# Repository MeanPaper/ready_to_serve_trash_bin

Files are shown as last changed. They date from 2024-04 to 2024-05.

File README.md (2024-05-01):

# Ready-to-serve Trash Bin
By collaboration of [Dongming Liu](https://github.com/MeanPaper), [Owen Xu](https://github.com/jinyuxu2), [Josh Litao](https://github.com/jlitao2) <br>
UIUC SP24 Senior Project Repository (Team 19) | January 2024 - May 2024

## About the Project
Throwing away trash is a simple task that many people take for granted. However, those with little to no mobility as a result of a disability, hospitalization, natural aging, or other health conditions struggle to carry out this necessary task. According to the CDC, 12.1 percent of U.S. adults have a mobility disability with serious difficulty walking or climbing stairs. As a result, these people either require an assistant to dispose of their trash for them, which may not always be feasible, or they are forced to hold their trash and let it accumulate by their side. Letting trash accumulate is a sanitary concern that could escalate into further problems. A trash bin could be placed next to the person, but this solution has various problems. An open trash bin would allow the odor of the trash to spread throughout the room, and a bin with a lid could pose difficulty for users whose conditions make them unable to open the lid directly with their hands or use their foot to press the pedal.

In order to eliminate the problems with existing trash bins for people with limited mobility, we propose a trash bin that would be ready to take a user’s trash once they perform a particular hand gesture to call it. A camera will be part of the motion and object detection system. This system to detect the hand gesture would be placed somewhere in the room where it would be able to monitor whether the user needs the trash bin to pick up their trash. The trash bin would be attached to a set of wheels to allow it to move. The lid of the bin would also be controlled to open and close. Once the camera detects that the user wishes to dispose of trash, the camera system would wirelessly communicate with the bin to prompt the bin to move toward the user. Upon arriving at the user, the lid would open, ready to collect the user’s trash. Once the user has disposed of trash into the bin, the lid would close, and the bin would return to its resting position. This solution simplifies the process of throwing trash by only requiring the users to call it and drop their trash into the bin.

## Project Video and Presentation
[Video](https://www.youtube.com/embed/DfU_nMM2fV8)<br>
[Presentation](https://courses.engr.illinois.edu/ece445/getfile.asp?id=23341)

## Usage 
### Hand Gesture Detection
For hand gesture detection, we recommend [Raspberry Pi 4B with 4GB RAM](https://www.raspberrypi.com/products/raspberry-pi-4-model-b/) with [64-Bit Raspberry Pi OS](https://www.raspberrypi.com/software/operating-systems/). The project uses this [Pi Camera](https://www.amazon.com/Arducam-Megapixels-Sensor-OV5647-Raspberry/dp/B012V1HEP4?th=1) in our project but other Pi Camera or USB camera should work as well. 

The required packages for the hand gesture detection can be found [here](https://github.com/MeanPaper/ready_to_serve_trash_bin/blob/main/hand-gesture-recognition-mediapipe/README.md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). To make package installation easier, we recommend setting up a virtual python environment using [`conda`](https://conda.io/projects/conda/en/latest/user-guide/getting-started.html) or [`venv`](https://docs.python.org/3/tutorial/venv.html). 

### Running Hand Gesture Detection and Training
More details can be found in the [hand-gesture-recognition-mediapipe](https://github.com/MeanPaper/ready_to_serve_trash_bin/blob/main/hand-gesture-recognition-mediapipe/README.md).

## Acknowledgements
- [Hand guesture recognition mediapipe](https://github.com/kinivi/hand-gesture-recognition-mediapipe/tree/main): computer vision for hand guesture recognition.
- [COMTool](https://github.com/Neutree/COMTool): easy-to-use debugging tool, for gathering data from serial port.

## References
- [QuickPID](https://github.com/Dlloydev/QuickPID/tree/master)
- [ESPAsyncWebServer](https://github.com/esphome/ESPAsyncWebServer)
- [ESP-IDF Programming Guide](https://docs.espressif.com/projects/esp-idf/en/stable/esp32s3/index.html)
- [ESP32-S3-WROOM-1 Datasheet](https://www.espressif.com/sites/default/files/documentation/esp32-s3-wroom-1_wroom-1u_datasheet_en.pdf)
- [L298](https://www.st.com/content/ccc/resource/technical/document/datasheet/82/cc/3f/39/0a/29/4d/f0/CD00000240.pdf/files/CD00000240.pdf/jcr:content/translations/en.CD000002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)
- [TPS56220x 4.5V to 17V Input, 2A Synchronous Step-Down Voltage Regulator in SOT-23](https://www.ti.com/lit/ds/symlink/tps562201.pdf)
- [TLV1117LV 1-A, Positive Fixed-Voltage, Low-Dropout Regulator](https://www.ti.com/lit/ds/symlink/tlv1117lv.pdf)
- [Low Dropout Linear Regulator](https://www.diodes.com/assets/Datasheets/AZ1117C.pdf)

## Academic Integrity
Please review the University of Illinois Student Code, particularly all subsections of [Article 1, Part 4 - Academic Integrity Policy and Procedure](https://studentcode.illinois.edu/article1/part4/1-401/).

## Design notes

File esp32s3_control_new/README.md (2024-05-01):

# MCU Code

## Pins (GPIOs) Setting
The pin settings are listed in `Proj_Setup.h`.

## WiFi Configuration
Change the following two lines in `esp32s3_control_new.ino` to let the MCU connect to different WiFi.
```cpp
const char * ssid = "your_actual_wifi_name"; 
const char * pass = "your_actual_wifi_password"; // if there is no wifi password, make it NULL
```
For retriving the MAC address of the MCU, use `WiFi.macAddress()`.

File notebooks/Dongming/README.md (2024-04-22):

# Dongming's Development Log

## Table of Contents
- [Dongming's Development Log](#dongmings-development-log)
  - [Table of Contents](#table-of-contents)
  - [Feburary 12, 2024](#feburary-12-2024)
    - [Project Design: Project Components](#project-design-project-components)
  - [Feburary 16, 2024](#feburary-16-2024)
    - [Project Design: Component Update](#project-design-component-update)
  - [February 20, 2024](#february-20-2024)
    - [Project Design: Motor Choice](#project-design-motor-choice)
  - [Feburary 27, 2024](#feburary-27-2024)
    - [MCU Code: Begin](#mcu-code-begin)
  - [March 02, 2024](#march-02-2024)
    - [MCU Code: MCU Pin Info and Driver Usage](#mcu-code-mcu-pin-info-and-driver-usage)
  - [March 04, 2024](#march-04-2024)
    - [MCU Code: Code Struture and MCU Pin Assignments](#mcu-code-code-struture-and-mcu-pin-assignments)
  - [March 09, 2024](#march-09-2024)
    - [MCU Code: Wireless Communication Code](#mcu-code-wireless-communication-code)
  - [March 13, 2024](#march-13-2024)
    - [MCU Code: Wireless Communication Testing Part 1](#mcu-code-wireless-communication-testing-part-1)
  - [March 16, 2024](#march-16-2024)
    - [MCU Code: FSMs](#mcu-code-fsms)
  - [March 17, 2024](#march-17-2024)
    - [MCU Code: Wireless Communication Testing Part 2](#mcu-code-wireless-communication-testing-part-2)
  - [March 18, 2024](#march-18-2024)
    - [MCU Code: Motor Control Code](#mcu-code-motor-control-code)
  - [March 26, 2024](#march-26-2024)
    - [Debug Customized PCB: Unable to Upload code to MCU with USB-to-UART](#debug-customized-pcb-unable-to-upload-code-to-mcu-with-usb-to-uart)
  - [March 29 to March 31, 2024](#march-29-to-march-31-2024)
    - [MCU Code: Motor Control - PID tunning](#mcu-code-motor-control---pid-tunning)
  - [April 05, 2024](#april-05-2024)
    - [PCB Testing: PCB v1](#pcb-testing-pcb-v1)
  - [April 08, 2024](#april-08-2024)
    - [PCB Testing: PCB v1 motor driver port two](#pcb-testing-pcb-v1-motor-driver-port-two)
    - [Project Design: Minor Update on Physical Design](#project-design-minor-update-on-physical-design)
  - [April 10, 2024](#april-10-2024)
    - [Project Production: Assembling and Testing](#project-production-assembling-and-testing)
  - [April 12, 2024](#april-12-2024)
    - [Project Production: Assembling Checklist](#project-production-assembling-checklist)
  - [April 17, 2024](#april-17-2024)
    - [Project Production: Product Testing without Raspberry Pi](#project-production-product-testing-without-raspberry-pi)
  - [April 18, 2024](#april-18-2024)
    - [Project Production: 3D Printed Box](#project-production-3d-printed-box)
  - [April 19, 2024](#april-19-2024)
    - [Project Production: Intergration Testing Part 1](#project-production-intergration-testing-part-1)
  - [April 20, 2024](#april-20-2024)
    - [Project Production: Intergration Testing Part 2](#project-production-intergration-testing-part-2)
  - [April 21, 2024](#april-21-2024)
    - [Project Production: Demo Setup](#project-production-demo-setup)
  - [EXTRA NOTE](#extra-note)

## Feburary 12, 2024
### Project Design: Project Components

Ready-to-serve trash bin has two big systems
- Motion and Object Detection System
- Trash Bin Control System

**Motion and Object Detection System:**
| Component | Usage |
| :--- | :--- |
| Raspberry Pi  | Image processing and communication with Trash Bin Control System  |
| Pi Camera | Image Capturing |

The Raspberry Pi Models I considered using:
- Raspberry Pi 4B RAM 4GB or 8GB
- Raspberry Pi 5 RAM 4GB or 8GB

Alternative to Raspberry Pi:
- OrangePi 4 / 5 with RAM 4GB or 8GB

If Raspberry Pi is not powerful enough, then the following would be considered:
- Nvidia Jetson board
- Intel processor single board computer
  
<br>

**Trash Bin Control System:**
| Component | Usage |
| :--- | :--- |
| [ESP32S3 WROOM 1 N16 ](https://www.espressif.com/sites/default/files/documentation/esp32-s3-wroom-1_wroom-1u_datasheet_en.pdf) | Wireless communication, control and drive motors with PWM signals |
| [L298N](https://www.digikey.com/en/products/detail/stmicroelectronics/L298N/585918) | Motor driver chip for amplifying the PWM from MCU based on the reference volatge |
| 12V DC Gear Motors (reversible) | Move the trash bin on the floor |
| 12V Linear Actuator (reversible)  | Open and close trash bin's lid  |

ESP32S3 WROOM 1 has a built-in wireless communication module; it is a good fit for this project. This MCU is part of the ESP32 S-series.<br>
***The alternative MCUs*** are still based on ESP32 but are in different series, for example, C-series or H-series.

The Motor driver chip L298N is very popular. One chip can control up to 2 DC motors. L298N supports up to a rated voltage of 40V and a max current of 2A, which is more than enough. L298N is hard to solder due to its package. Also, L298N is relatively expensive. <br>
***The alternative motor drivers*** are [A4950](https://www.digikey.com/en/products/detail/allegro-microsystems/A4950ELJTR-T/2626340) or [DRV8870](https://www.digikey.com/en/products/detail/texas-instruments/DRV8870DDAR/5455925). Both have wide operating ranges. The drawback is that each motor driver can only control 1 motor.

The 12V linear actuator only does 3 motions: open, hold, and close. Position tracking is not necessary, so the 12V linear actuator only needs to has two terminals.

The 12V DC Motors needs to provide speed tracking interfaces. One mechanism of speed tracking will be to used hall encoders. 

The power subsystems for these two big systems are ignored. My teammate will come with the power circuit/subsystem for the project.

**TODO:**
- Finalize all components for this project (not including battery)
- Learn how to detect speed using hall encoders
- Skim through the data sheet of ESP32S3 and get familiar with the pins on ESP32S3

## Feburary 16, 2024
### Project Design: Component Update

**Updates:**
- Raspberry Pi 4B with 4 GB. The system is Raspberry Pi OS (64-bit)
- Camera module (5M pixel somana camera module with OV5647)
- Power for Raspberry Pi: Raspberry Pi 4 official charger
- 12V linear actuator is finalized. The part and its purchase link are updated in the component list. 
- 12V DC motors are finalized. The part and its purchase link are updated in the component list. JGB37-520 Hall Encoder Miniature Brushed DC Motor (178 RPM).

The MCU code will be developed on a development board with ESP32S3-WROOM-1-N8 module. For motor drivers, I will use the L298N breakout boards. 

Tentative setup for the project testing:
| Components | Quantity |
| :--- | ---: |
| ESP32S3-WROOM-1 Dev Board | 1 |
| L298N module | 2 |
| Breadboard | 1 |
| Jumper wires | 30 |

Note: the jumper wires might be a bit more, but they are for rewiring.

## February 20, 2024
### Project Design: Motor Choice

The motor needs to provide enough power to move the bin. Therefore, we need to come up with a minimum theoretical power of a motor.

|  Variable  | Comment |
|:--- |:---|
| $\tau_{w}$ | torque of a motor (in Nm) |
| $R_{w}$ | wheel radius (in m) |
| $\mu_{w}$  | static friction coefficient of the wheel against the floor |
| $\mu_{c}$  | static friction coefficient of the metal caster against the floor|
| $m_{T}$ | total mass (in kg) |
| $F_{N}$ | normal force (in N) |
| $F_{wf}$ | static friction of the wheel (in N) |
| $F_{cf}$ | static friction of the mastern (in N) |
| $g$ | gravitational acceleration constant (m/s<sup>2</sup>) |

Two DC gear motors at the same position can provide:

$2\tau_{w}=F_{wf} * R_w$

In rolling without slipping, the static friction of the wheels cannot exceed the static friction of the total mass. With two type of wheels (one in rubber, and the other in metal), we have:

$F_{wf} \leq F_N * (\mu_w + \mu_c)$

Using Newton's Second Law:

$F_g = m_T * g$

since the bin does not accelerate up and/or down, $F_g = F_N$

Therefore, the static friction of the total mass is:

$m_T * g * (\mu_w+\mu_c)$

Combing the inequality:

$\frac{2\tau_w}{R_w} \leq m_T * g * (\mu_w + \mu_c)$

$\frac{2\tau_w}{R_w * g * (\mu_w + \mu_c)} \leq m_T$

The wheel radius of our wheel is about 0.0762 m. Assuming that the static coefficients of both wheels are approximately 0.5, and the total mass is about 2.3kg to 2.8kg, we need both motors to provide a torque of at least 0.373 Nm.

Also, we want the bin to move at human walking speed, which should be no more than 1.2 m/s. 

$\text{motor RPM} \leq \frac{1.2 * 60}{\pi * d}$

Based on the theoretical result, the motor we picked previously might not be able to move the bin. So we switch to JGB37-520 Hall Encoder Miniature Brushed DC Motor (60 RPM).

## Feburary 27, 2024
### MCU Code: Begin

MCU code quick break down:
- Motor control module
    - DC motors
    - linear actucator
- Wireless communication module
    - WiFi
    - Service API

The DC motors need to use 5 pins (`PWM`, `D1`, `D2`, `HALL_A`, `HALL_B`)
| Pin Name  | Description |
| :---: | :--- |
| `PWM` | PWM signal to the motor driver|
| `D1`  | Direction control 1 (for H-bridge) to the motor driver|
| `D2`  | Direction contorl 2 (for H-bridge) to the motor driver|
| `HALL_A` | Hall encoder phase A from the motor|
| `HALL_B` | Hall encoder phase B from the motor|
  
The linear actuator need to use 3 pins (`PWM`, `D1`, `D2`)
| Pin Name  | Description |
| :---: | :--- |
| `PWM` | PWM signal to the motor driver|
| `D1`  | Direction control 1 (for H-bridge) to the motor driver|
| `D2`  | Direction contorl 2 (for H-bridge) to the motor driver|

**Quick Review on H-bridge:** <br>
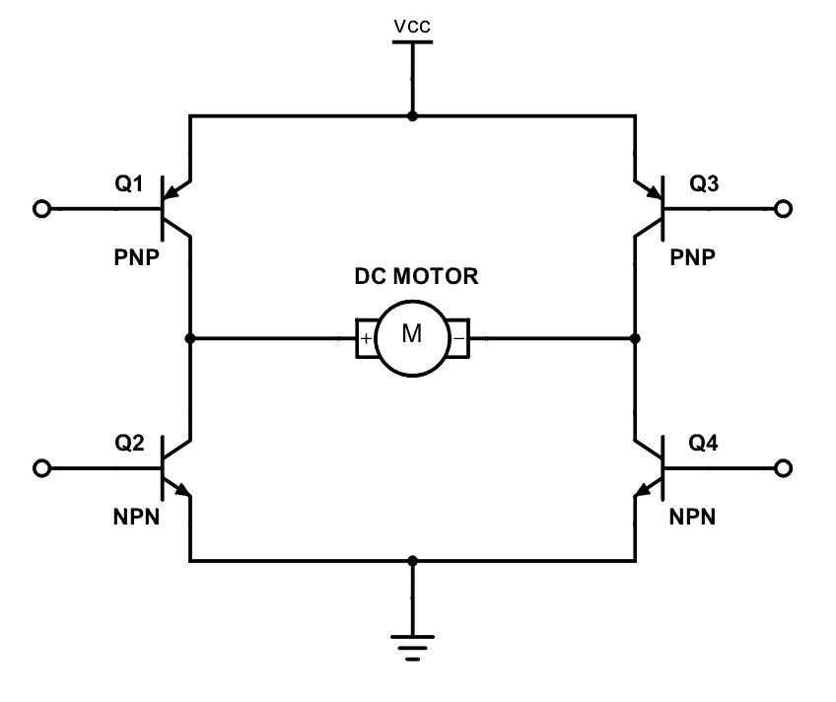
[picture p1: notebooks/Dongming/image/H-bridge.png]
H-bridge Schematic

<br>
`Q1` and `Q4` are controlled by one of the `D`'s; `Q2` and `Q3` are controlled by the other `D`. If `Q1 = Q4 = HIGH` and `Q2 = Q3 = LOW` makes the motor turn clockwise (assuming), then `Q1 = Q4 = LOW` and `Q2 = Q3 = HIGH` makes the motor turn counterclockwise.

In [L298N](https://www.st.com/content/ccc/resource/technical/document/datasheet/82/cc/3f/39/0a/29/4d/f0/CD00000240.pdf/files/CD00000240.pdf/jcr:content/translations/en.CD000002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), it has two H-bridges. The IN1 and IN2 (or IN3 and IN4) can be mapped to D1 and D2. The MCU can send logic HIGH and LOW via D1 and D2. This effectively controls the state of each pair of switches, similar to the previous description.

**Quick Review on PWM** 
<br>
With PWM control, we can limit the voltage (and current) delivered to the motors and linear actuators. 
<br>
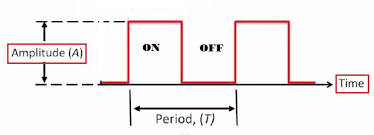
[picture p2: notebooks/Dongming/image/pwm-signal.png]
PWM signal diagram


The Duty cycle is the percentage of ON time with respect to the entire period (like the diagram shown above). So,

$\text{Duty Cycle} = \frac{T_{ON}}{T_{Period}}$

and the average voltage over time is

$V_{avg} = \text{Duty Cycle} * V_{amplitude}$

For example, given the max voltage is 12V and the duty cycle is 50%, the average voltage will be 6V. 

With PWM control and constant DC source, we can change the voltage delivered by changing the duty cycle of the PWM signal, allowing the motors and linear actuators to run at different speeds.

**Quick Start on Hall Encoder**

One popular speed measuring method is to use the hall encoders. Most DC motors with hall encoders have two phases: A and B. 

By observing the difference between the two phases, we can determine the direction the motors are turning and approximate the speed of the motors. One method is 

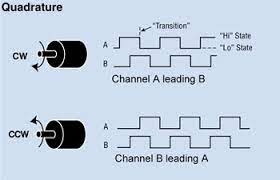
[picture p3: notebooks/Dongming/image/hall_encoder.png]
Quadrature hall encoder


An nice article on Speed Measurement (in Chinese): https://zhuanlan.zhihu.com/p/350368518

I will use the M-method for speed measurements. The unit of speed is RPM.

The computation can be done as the following:

$\text{total pulse count} = \text{PPR} * \text{reduction ratio}$

$\text{output shaft speed} = \frac{\text{pulse count}}{\text{total pulse count}} * \frac{1000}{\text{sample time (ms)}} * 60$

This computation will approximate the current speed of the motors (in RPM) based on the pulse counts.

**TODO:**
- Set up wireless communication between the ESP32S3 chip and other edge devices
- Figure out how to control motor using L298N

## March 02, 2024
### MCU Code: MCU Pin Info and Driver Usage

**Quick Check of ESP32S3-WROOM-1**

The official documentation of ESP32S3-WROOM-1: https://www.espressif.com/sites/default/files/documentation/esp32-s3-wroom-1_wroom-1u_datasheet_en.pdf

The technical manual of ESP32S3-WROOM-1: https://espressif.com/documentation/esp32-s3_technical_reference_manual_en.pdf

Some pins might not be available for programming:

For modules with Octal SPI PSRAM, i.e., modules embedded with ESP32-S3R8 or ESP32S3R16V, pins IO35 (GPIO 35), IO36 (GPIO 36), and IO37 (GPIO 37) are connected to the Octal SPI PSRAM and are not available for other uses.

Strapping pins are used to set up the MCU mode:
- Chip boot mode -- GPIO 0 and GPIO 46
- VDD_SPI voltage -- GPIO 45 
- ROM messages printing -- GPIO 46 
- JTAG signal source -- GPIO 3

Section 3.3.1 specifies the download mode setup for the MCU. GPIO 0 needs to be set to logic low to enable Joint Download Boot (maybe we need to have some connections in the schematic to configure the MCU mode)

Section 3.3.4 specifies the setup of the GPIO 3 for enabling JTAG (useful for debugging).

Avoid using GPIO 39 and above. Jtag uses GPIO 39 ~ 41. GPIO 42 and 43 are used for downloading code. We will use a USB-to-UART bridge module to manage auto-download rather than solder a bridge IC on board.

Something need to pay attention when using WiFi ([A useful website](https://nu-ll.github.io/2022/06/05/ESP32%E5%BC%95%E8%84%9A%E4%BD%BF%E7%94%A8%E6%B3%A8%E6%84%8F%E4%BA%8B%E9%A1%B9/))

GPIOs associated with ADC2 channels may be occupied when WiFi is in use. If our MCU cannot read/write to those pins when WiFi is enabled, we need to use some other pins. GPIOs associated with ADC1 channels can be an alternative in case that we need to use the ADC functionalities or use them for other purposes.

ESP32S3 have two different wireless communication method between devices (assuming the other device is not a ESP32 board).
- Bluetooth (normal bluetooth / low power bluetooth)
- WiFi 

The WiFi communication generally has a wider range. So it would be a good option in our case. To make the communication more standardized, I will use HTTP protocols. HTTP protocols are built on top of TCP, and TCP can minimize packet loss in our communication. However, the efficiency of wireless communication might decrease a bit. An alternative would be using UDP. UDP can provide great efficiency under good network conditions but may result in a larger packet loss if the network conditions are not desired.

**L298N setup**

L298N Datasheet: https://www.st.com/resource/en/datasheet/l298.pdf

The L298N is a dual full-bridge driver. Inside L298N, there are two full H-bridge drivers. Previously, I have investigated [how H-bridge works](#mcu-code-begin), I can just connect the IC based on that. Since I was not too familiar with power circuit, I handed this part to my EE teammate. 

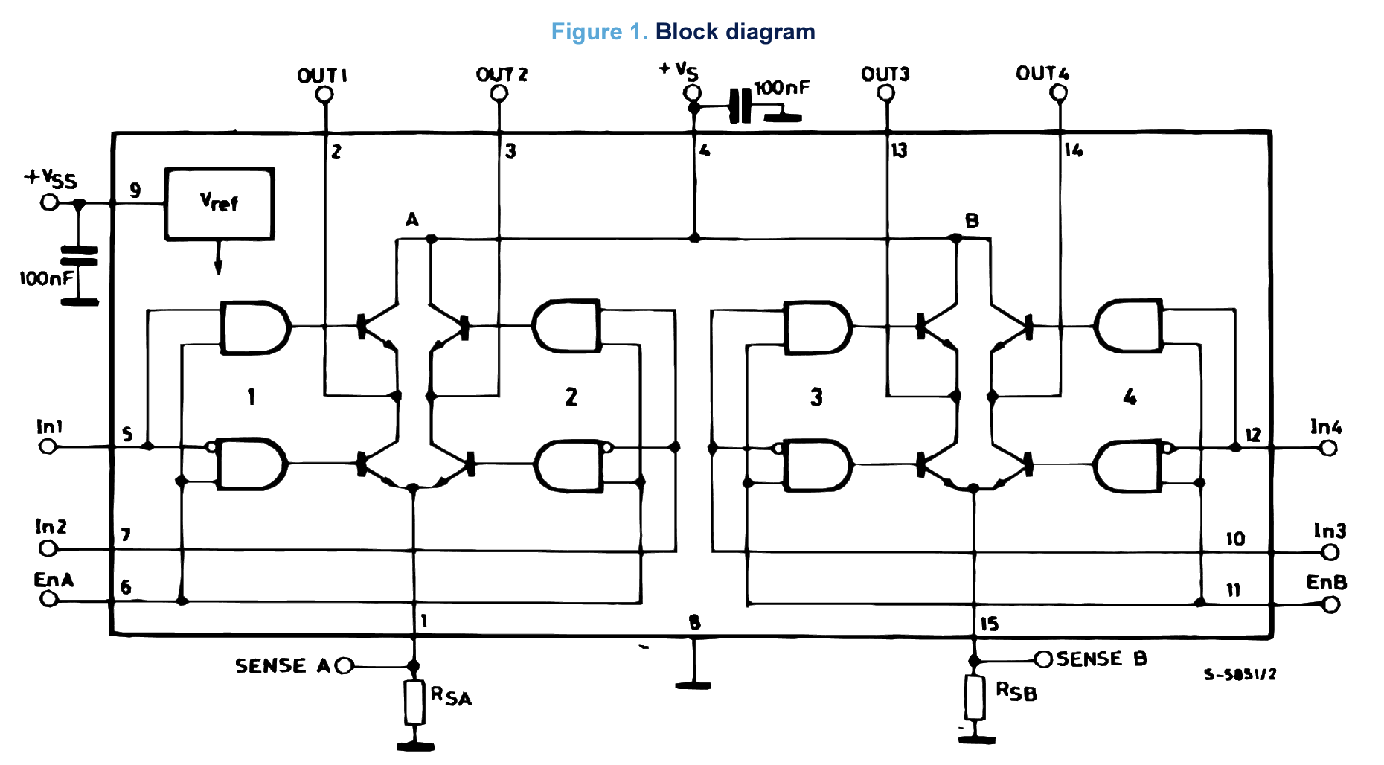
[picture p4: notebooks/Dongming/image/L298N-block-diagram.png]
L298N block diagram


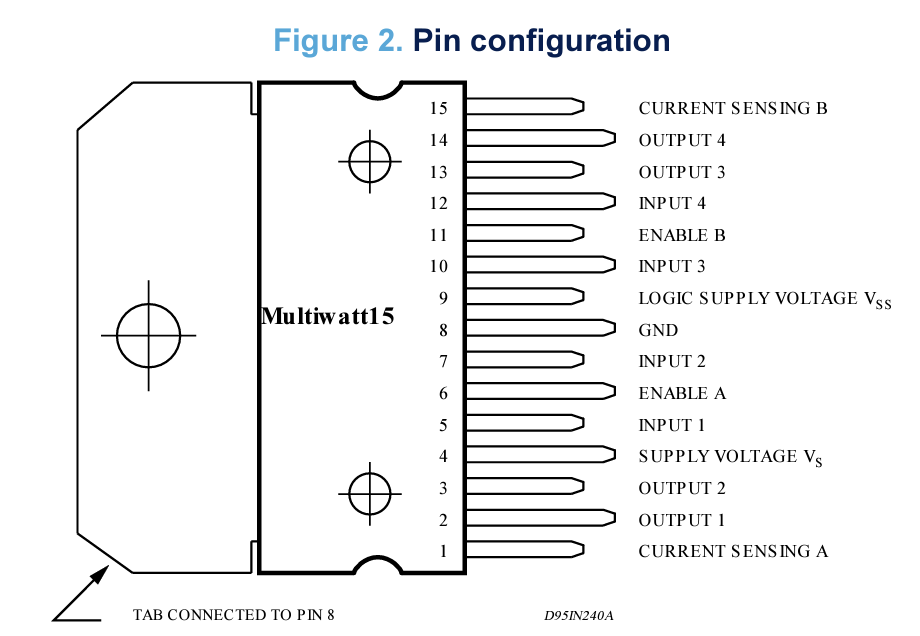
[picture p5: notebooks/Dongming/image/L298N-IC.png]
L298N IC


ENABLE A, IN 1, IN 2, OUTPUT 1, and OUTPUT 2 control the first motor. <br>
ENABLE B, IN 3, IN 4, OUTPUT 3, and OUTPUT 4 control the second motor.

The IN's control the direction of the motors. ENABLE's determine if the motor should be running of not. It is recommended to drive the ENABLE's with PWM to achieve speed control. OUTPUT's control the current outputing to the motors.

**TODO:**
- Assign MCU pins for programming
- Draft the wireless communication for the MCU

## March 04, 2024
### MCU Code: Code Struture and MCU Pin Assignments 

Files and brief:
- `esp32s3_control_new.ino`: main function, containing initial set up, MCU loop, and other main loop related variables/ helper functions/ handlers.
- `DCMotor.h`: a header file, containing a DCMotor class
- `DCMotor.cpp`: contains all function definitions of DCMotor class
- `Proj_Setup.h`: a header file, containing MACROS, enum, structures, and all helper functions in the projects
- `Proj_Setup.cpp`: contains all function definitions of helper functions and global variables 

Here is the finalized version of the pin assignments
```cpp
/**
  * DC Motor Control 
  * MT# = motor #
  * D1 and D2 are used for H-bridges control
  * D1 (out) - motor direction control 1
  * D2 (out) - motor direction control 2
  *
  * HALL_A and HALL_B are the pins for motor hall sensors, 
  * used for determining motor speed and direction
  * HALL_A (in) - hall sensor phase A
  * HALL_B (in) - hall snstor phase B
  *
  * PWM is the PWM signal for the motor driver, voltage/speed control 
  * PWM (out) - output 
  *
  */

// motor 1 control pins
#define MT1_D1      11
#define MT1_D2      12
#define MT1_PWM     13
#define MT1_HALL_A  16
#define MT1_HALL_B  18

// motor 2 control pins
#define MT2_D1      38
#define MT2_D2      35
#define MT2_PWM     14
#define MT2_HALL_A  17
#define MT2_HALL_B  21

/**
  * Linear Actuator
  * D1 and D2 are used for H-bridges control
  * D1 (out) - motor direction control 1
  * D2 (out) - motor direction control 2
  *
  * PWM is the PWM signal for the motor driver, voltage/speed control 
  * PWM (out) - output 
  *
  */
// linear actuator pins 
#define Ln_Act_D1   36
#define Ln_Act_D2   37
#define Ln_Act_PWM  15
```
The GPIOs listed here will connect to the corresponding components on the customized PCB.

In ESP32, the LED control (LEDC) peripheral is primarily designed to control the intensity of LEDs, but it can also be used to generate PWM signals. The PWM controller can automatically increase or decrease the duty cycle gradually, allowing for fades without any processor interference. We can control PWM output frequency, resolution, and channels of LEDC in setup to ensure that the PWM is tailored to the project's components. The library header is `esp32-hal-ledc.h`. In Arduino-ESP32 core, we can use `analogWrite` (a function in Arduino Analog I/O) to output PWM signals on a specific pin. However, the Arduino Analog I/O only has a few parameters can be configured. 

```cpp
/* PWM control section */

// PWM channels
#define CHAN_MT_ONE 1
#define CHAN_MT_TWO 2
#define CHAN_LN_ACT 3

// PWM control params
#define RESOL   8                 // resolution of the PWM signal
#define MT_FREQ 200               // motor channel frequency, this may not work
#define LA_FREQ 200               // linear actuator frequency
#define MAX_PWM pow(2, RESOL)-1   // the max duty cycle
```
**TODO:**
- Draft the wireless communication for the MCU

## March 09, 2024
### MCU Code: Wireless Communication Code

The wireless communication can be break into 3 steps:
1. MCU establishes a WiFi connection (with a device/router)
2. MCU creates a web server with different APIs 
3. MCU listens for requests coming from the client device (in the project, the client device is the Raspberry Pi)

**WiFi Connection**

Arduino IDE's built-in library `WiFi` can help ESP32S3 establish a WiFi connection with a router or make ESP32S3 a WiFi access point. The `WiFi` class has two modes `softAP` and `STA`.
- `softAP`: makes ESP32S3 a WiFi access point
- `STA`: ESP32S3 will connect to the WiFi router

`STA` is more suitable for the project. Since ESP32S3 is connected to a WiFi router, and the WiFi router's signal is strong, ESP32S3 can communicate with the WiFi router pretty much everywhere. 

The communication mechanism:
```txt
ESP32S3 <----- Data -----> Router <------ Data ------> Devices
```

The ESP32S3 module will start a web server and expose its IP address in the WiFi network. The devices under the same WiFi network can communicate with the ESP32S3 via ESP32S3's IP address. Here is how WiFi connection between ESP32S3 and router establishes:

```cpp
#include <WiFi.h>

const char * ssid = "IllinoisNet_Guest"; // wifi name of the wifi esp32s3 needs to connect
const char * pass = NULL;                // wifi password, if wifi does not have password, leave it null

void setup(){ 
  Serial.begin(9600);                    // setup serial with a baud rate, for serial printing
	WiFi.begin(ssid, pass);                 
	Serial.printf("Connecting to %s", ssid);
	while(!WiFi.isConnected()){            // attempt to connect
	  Serial.print(".");
	  delay(1000);
	}
	Serial.println();

  // output IP address of ESP32S3 in the current wifi network
	Serial.println("WiFi IP: ");
	Serial.println(WiFi.localIP());

  // some code for initialization (pin setup, motors, sensors, etc)
}

void loop(){
  // some code for ESP32S3 main loop
}
```

ESP32S3 cannot directly access UIUC's school network (`IllinoisNet_Guest` or `IllinoisNet`). To allow ESP32S3 to access UIUC's school network, ESP32S3 must be added to the device list under a student's account. To register ESP32S3 and add it to the device list, go to https://go.illinois.edu/illinoisnetguest and log in, click on "Register a New Device". The device registration requires the MAC address of the device. To get ESP32S3's MAC address, we can add a line in the `setup` function:
```cpp
Serial.println(WiFi.macAddress());
```

**Web Services**

The main communication protocol between ESP32S3 and the connected devices in the project is HTTP. It might not be the optimal solution, but it works. To optimize the performance of handling HTTP requests on ESP32S3, I created an async web server on the ESP32S3 using `ESPAsyncWebServer`. The advantage of this approach is that the async web server is managed by an event loop. The main program would not be blocked by the request handling of the async web server. In this case, the web server and main program (motor controls) can run concurrently on a single core of ESP32S3. ESP32S3 has two cores. Technically, I can create two threads (one for the main program and one for web services). The MCU code will be more complex and challenging because there is quite a lot of data shared between two threads and synchronization is required. It is also possible that the true multithread program might have a worse performance due to synchronization overhead and other reasons.

To create an async web server on ESP32S3, we need to include the library `ESPAsyncWebServer.h` in our program and then create an `AsyncWebServer` object:
```cpp
AsyncWebServer server(80); // start a web server at port 80, HTTP generally uses port 80
```

The device (Raspberry Pi) needs to control the movement and the lid of the bin. To make the control easier, I created a list of APIs:

- `stop_motors`<br>
  Description: Stop the movement of the bin (not include the lid movement)

  Parameters: None
  
  Response:
  - a json object containing current state `{state: "STOP" | "LID" }`

- `set_speed`<br>
  Description: Set the speed of motors for a specific duration. Left and right motors can adjust to different speed

  Parameters:
  - `duration`(long int): motor control duration in ms [optional, default: 0]
  - `speedLeft`(float): left motor speed [optional, default: 0]
  - `speedRight`(float): right motor speed [optional, default: 0]

  Response:
  - a json object containing current state `{state: "YOLO" | "LID" }`

- `set_lid`<br>
  Description: Open the lid of the bin
  
  Parameters: None

  response:
  - a json object containing current state `{state: "LID"}`
    
- `move`<br>
  Description: Move the bin forward or backward with a specific speed for a specific duration

  Parameters:
  - `duration`(long int): motor control duration in ms [optional, default: 5000]
  - `speed`(float): moving speed [optional, default: 0]
  - `direction`(string):  "forward"/"backward" [optional]

  Response:
  - a json object containing current state `{state: "FORWARD" | "BACKWARD" | "LID" }`
  
- `turn`<br>
  Description: Turn the bin left or right with a specific speed for a specific duration

  Parameters:
  - `duration`(long int): motor control duration in ms [optional, default: 5000]
  - `speed`(float): turning speed [optional, default: 0]
  - `direction`(string): "left"/"right" [optional]

  Response:
  - a json object containing current state `{state: "LEFT" | "RIGHT" | "LID" }`

*A design choice for state machine implementation later:* <br>
When `set_lid` is called, the main control program enters the state `LID`. In the `LID` state, any incoming requests will be blocked, and all handlers will respond `{state: "LID"}`. In the `LID` state, the bin must stop. The main control program will leave the `LID` state once the `LID` is completely closed.

Web services handlers on ESP32S3:
```cpp
// web service handlers
void handleRoot(AsyncWebServerRequest *);          // for connection testing
void handleStopMotors(AsyncWebServerRequest *);    // stop_motors
void handleSetSpeed(AsyncWebServerRequest *);      // set_speed
void handleLid(AsyncWebServerRequest *);           // set_lid
void moveForwardBackward(AsyncWebServerRequest *); // move
void turnLeftRight(AsyncWebServerRequest *);       // turn
```

Web services handler general definition in the project:
```cpp
void some_handler(AsyncWebServerRequest * request){
  // some local variables

  // request data parameter checking
  // depends on the API, the handler can have no  hecking or more than one checking
  if(request->hasParam("something", true)){
    // update control data based on the request data
  	something = request->getParam("something", true)->value().toInt();
  }

  // some updates on the control variables (global / local)

  // setting up response 

  request->send(200, "application/json", response);
}
```
Almost all handlers create a `JsonDocument` object. `JsonDocument` is a class in a library called `ArduinoJson.h`. This class makes JSON object creation much easier. When handlers need to send back a response, they can convert the JsonDocument to a JSON object string using the `serializeJson` function. 

Intialize all the APIs and start asyc web server:
```cpp

  // include this chunk of code in void setup(), after WiFi setup
  // async server handling
  server.on("/", HTTP_GET, handleRoot);
  server.on("/stop_motors", HTTP_POST, handleStopMotors);
  server.on("/set_speed", HTTP_POST, handleSetSpeed);
  server.on("/set_lid", HTTP_POST, handleLid);
  server.on("/move", HTTP_POST, moveForwardBackward);
  server.on("/turn", HTTP_POST, turnLeftRight);

  // turn on the web server 
  server.begin();
```

After doing all the setup, all devices in the same wifi network can interact with the web server on ESP32S3. To interact with the server, the device can send data via `http://ESP32S3_IP_ADDRESS/:path`. An easy way to verify whether the web server is working or not is to go to `http://ESP32S3_IP_ADDRESS/` on the laptop's browsers. This triggers the root handler of the ESP32S3 web server. The relative path of the root is `/`. The browser will show the text, "Welcome to ESP32-S3". Here is the definition of the root handler of the ESP32S3 web server:
```cpp
void handleRoot(AsyncWebServerRequest * request){ // use this for debugging I guess
  Serial.println("Request root");
  request->send(200, "html", "<h1>Welcome to ESP32-S3</h1>");
}
```
I am writing a Python script using `httpx` to interact with the ESP32S3 web server. The goal of the script is to test the functionalities and behaviors of the web server. 

**Additional materials:**
- An article on setting up connection between ESP32S3 and Router: [Link](https://www.upesy.com/blogs/tutorials/how-to-connect-wifi-acces-point-with-esp32)
- Arduino WiFi Reference: [Link](https://www.arduino.cc/reference/en/libraries/wifi/)
- ESPAsyncWebServer Reference: [Link](https://github.com/esphome/ESPAsyncWebServer)

**TODO:**
- Test all the web server APIs
- Write the motor control code

## March 13, 2024
### MCU Code: Wireless Communication Testing Part 1

Based on our plan, we can break down the testing plan as the following parts:
- Connecting to WiFi network and verifying if the IP Address can be `ping`
- Testing the async web server and see if the APIs receives the request and parse the request data

The first image shows that ESP32S3 has successfully connected to the wifi network. Devices under the same wifi network can ping the IP address of ESP32S3 (shown in the second image).

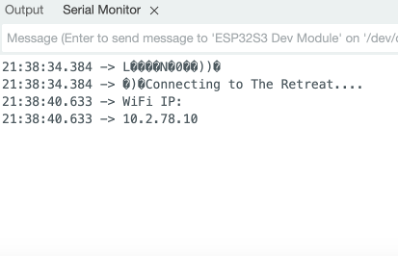
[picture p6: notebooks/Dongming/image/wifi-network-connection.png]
esp32s3 connects to wifi network

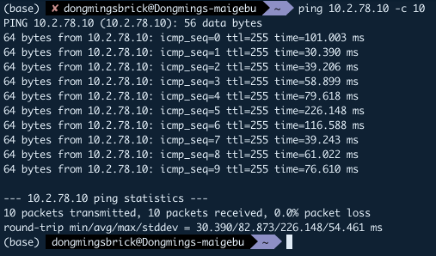
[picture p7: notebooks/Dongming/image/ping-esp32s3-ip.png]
ping the IP address of ESP32S3


Then, we can move on and test the web service APIs once all the APIs are done.

**TODO:**
- Create control state machine for the trash bin system 
- Finish and test all the web service APIs

## March 16, 2024
### MCU Code: FSMs

The control flow of the MCU can be shown as a finite state machine. The main loop of the MCU will manage this finite state machine.

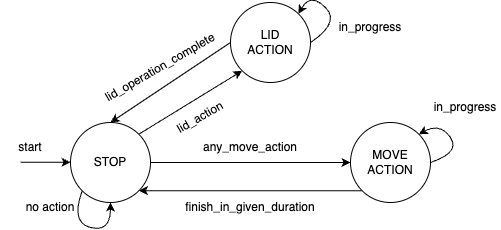
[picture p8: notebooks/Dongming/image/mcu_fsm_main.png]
the main finite state machine of the control


The MCU begins in the `STOP` state. Based on the client's requests, the MCU can only transition to `LID ACTION` or `MOVE ACTION` states. When MCU is in `LID ACTION` and `MOVE ACTION`, it only returns to `STOP` until the operation of the action is done. The duration of the operation is specified by the client. 

The `MOVE ACTION` state is broken down into 5 operations: `FORWARD`, `BACKWARD`, `LEFT`, `RIGHT`, and `YOLO`. To command the MCU to perform one of the operations, the client needs to format the request accordingly and call the appropriate APIs provided by the MCU. The first 4 operations, as the state name suggested, move the trash bin forward/backward or turn the trash bin to the left/right. `YOLO` is a special operation that allows the client to adjust the speed of each motor independently, and accomplish more flexible motion, for example, moving the trash bin diagonally. So all the web service APIs should be able to change the states of the main control state machine. Only `handleLid` can change the state of the lid operation.

Let's use `handleLid as example`
```cpp
void handleLid(AsyncWebServerRequest * request){
	
	#if (DEBUG)
  	Serial.println("Request lid operation"); // only for debug purposes
	#endif

  	// local variables
  	JsonDocument doc;
	String response;
	
	// set up operation control signals
  	stopDCMotor();
  	setLid();

	// set up response data to the client
  	current_state = LID;                         // change the main FSM to LID state
	doc["state"] = stateToString(current_state); // a helper function: convert MACRO to string
	serializeJson(doc, response);

  	// time recording, and send a response to the remote control device
	recordTime = millis();
  	request->send(200, "application/json", response);
}
```

In the project design, once the trash bin is close to the user. The trash bin will open the lid, hold the lid open for about 30 seconds, and close the lid. The `LID ACTION` state presents this sequence of operations. When the MCU is in `LID ACTION`, it rejects other operations until it returns to the `STOP` state. Since the `LID ACTION` has a sequence of operations, it can also be shown as a state machine.

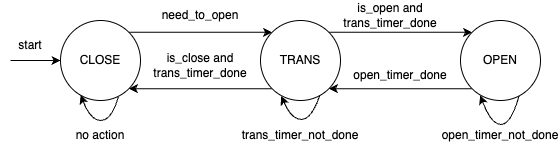
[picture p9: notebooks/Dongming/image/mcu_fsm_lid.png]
the lid operation finite state machine


The MCU lid control begins with the `CLOSE` state, sets the `is_open` flag, and unsets the `is_close` flag. Once the client requests to use the lid, the control transitions to the `TRANS` state via `need_to_open`. Since both `CLOSE` and `OPEN` can transition to `TRANS` and `TRANS` can go to either state after finishing its timer countdown, `is_open` and `is_close` flags are in use to help the `TRANS` state determine the next state it needs to go. To avoid ambiguity, both flags cannot be set simultaneously (i.e., both flags cannot be both `false`/`true`). With a set `is_open` flag, `TRANS` moves to `OPEN`. With a set `is_close` flag, `TRANS` moves to `CLOSE`. In the `OPEN` state, the MCU unsets the `is_open` flag and sets the `is_close` flag. After the timer countdown is complete, `OPEN` moves back to `TRANS`, and then `TRANS` moves back to `CLOSE`.

The code of the main state machine is in the `loop` function in `esp32s3_control_new.ino`.<br>
The code of the lid operation state machine is in the `checkLid` function in `Proj_Setup.cpp`.

**TODO:**
- Test all the web service APIs 
- Write the code for motor control

## March 17, 2024
### MCU Code: Wireless Communication Testing Part 2

I have written a simple test code for sending requests to the ESP32S3 and receiving responses from the ESP32S3. Since the CV part of the project is entirely in Python, the test code will also be written in Python. If the test code works well, I can easily implement it in the CV part of the project. 

More details about the test code can be found in `debugging/esp32s3_web_test.ipynb`

Here are some of the example tests:

Stop motor test and result:

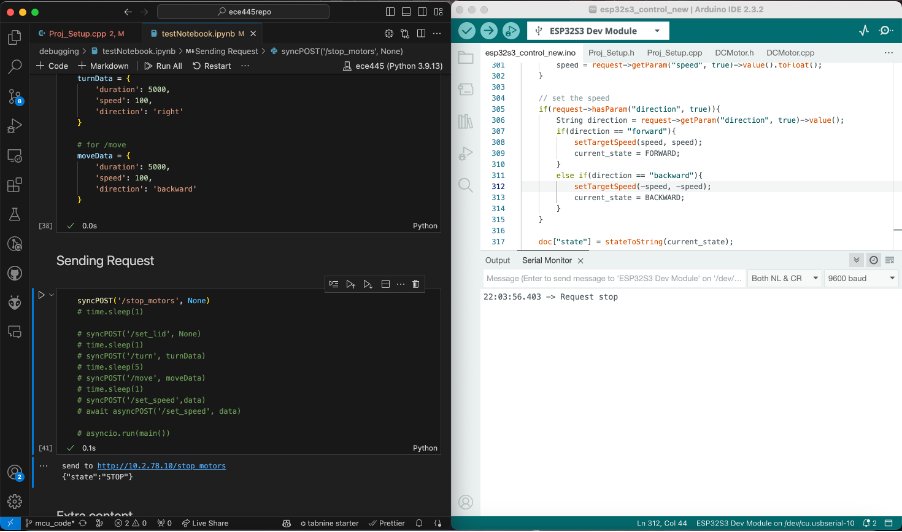
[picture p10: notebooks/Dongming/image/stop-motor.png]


Set speed test and result:

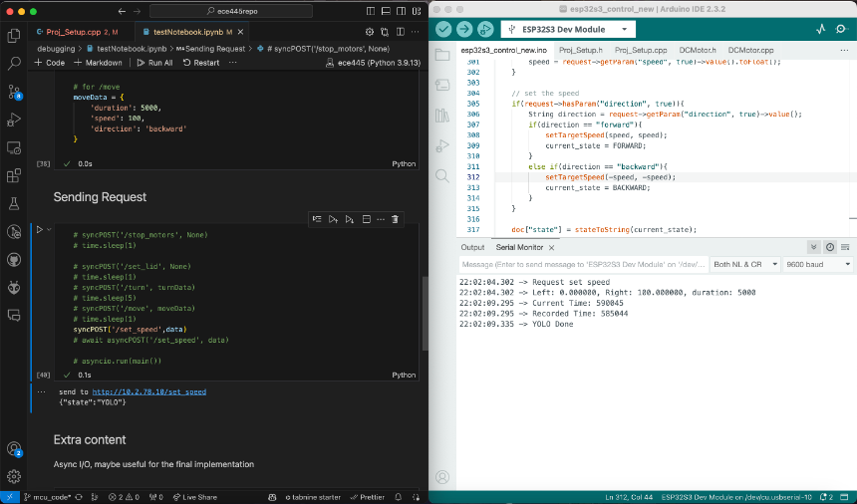
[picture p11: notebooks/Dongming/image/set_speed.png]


Move forward test and result:

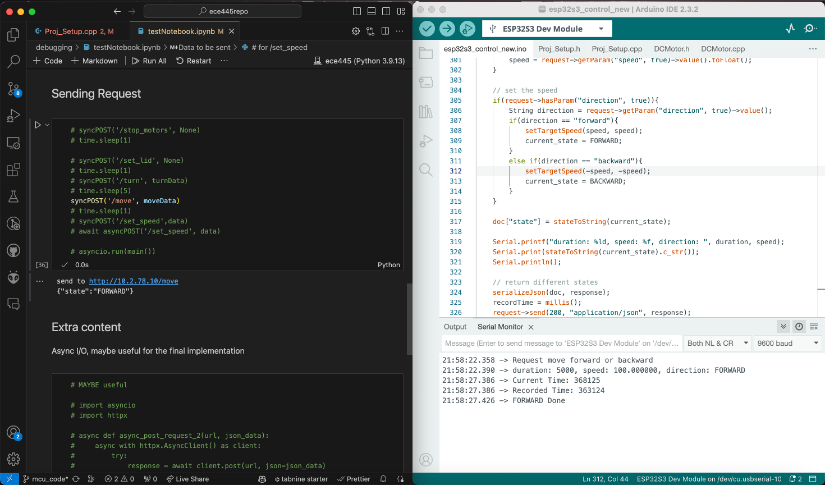
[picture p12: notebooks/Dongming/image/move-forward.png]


Move backward test and result:

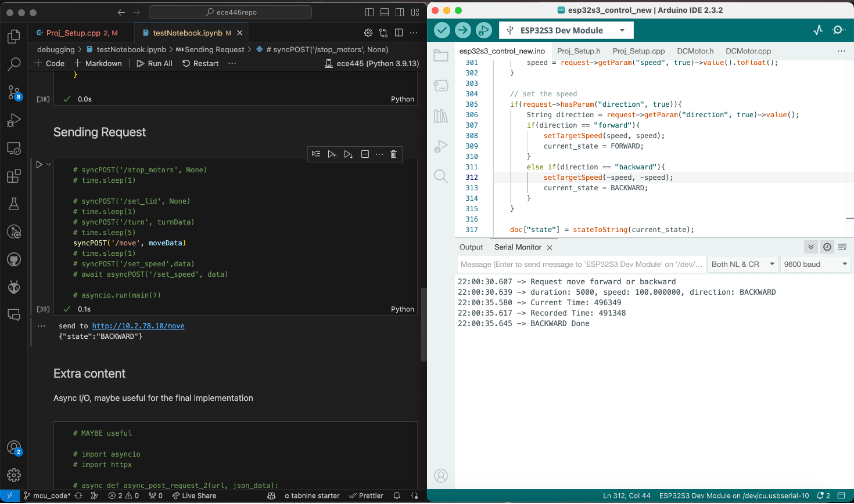
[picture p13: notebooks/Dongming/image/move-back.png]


Turn left test and result:

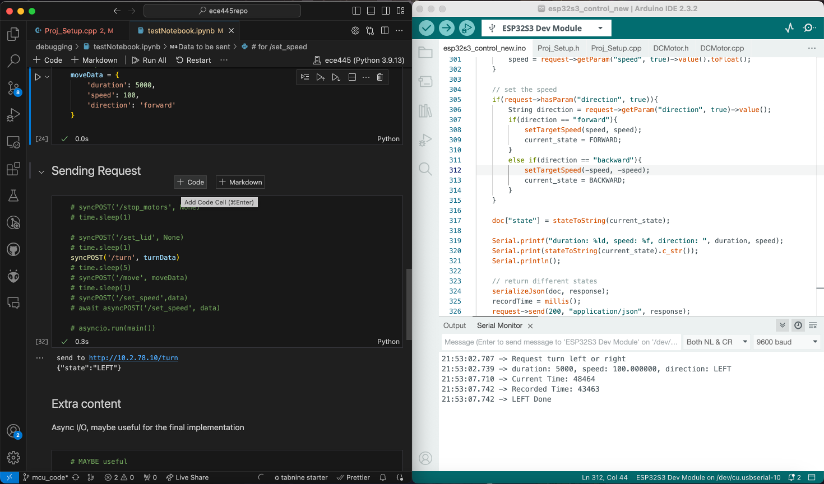
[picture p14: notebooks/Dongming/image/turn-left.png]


Turn right test and result:

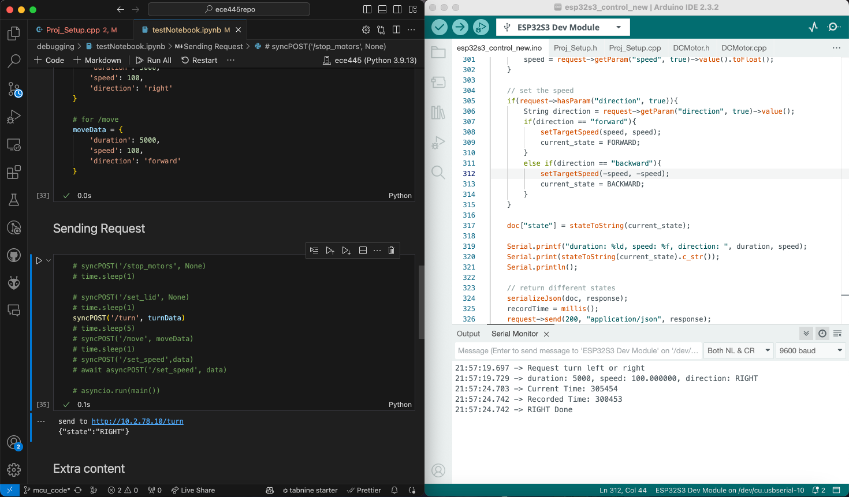
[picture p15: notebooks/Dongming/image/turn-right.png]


Set lid operation test and result:

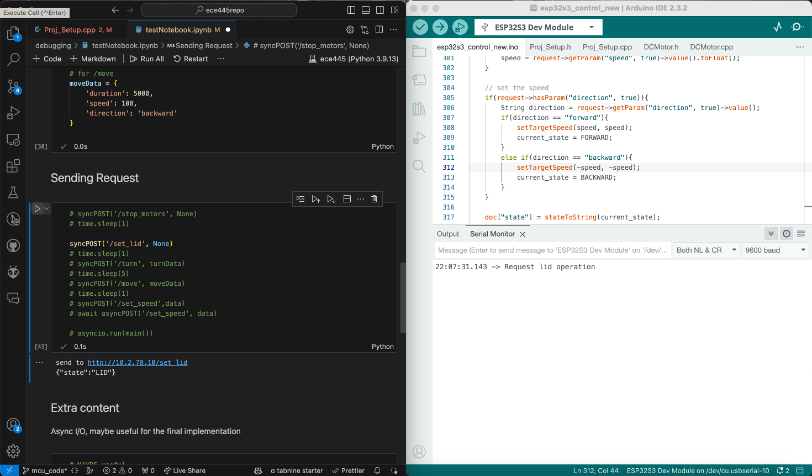
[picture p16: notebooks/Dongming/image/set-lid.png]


The clients can access all the APIs, and all the APIs can parse the request data correctly and send back the response promptly. The average response time is less than 1 seconds, which is within our acceptable range.

**TODO:**
- Write the code for motor control

## March 18, 2024
### MCU Code: Motor Control Code

There are two types of motor the project uses:
- DC gear motor with hall encoders
- Linear actuator

Based on the previous [PIN assignment](#mcu-code-code-struture-and-mcu-pin-assignments):
- DC gear motor with hall encoders: 5 pins (1 for pwm, 2 for direction, 2 for hall encoders)
- Linear actuator: 3 pins (1 for pwm, 2 for direction)

`DCMotor.h` and `DCMotor.cpp` contain all the information about setting up the DC gear motor with hall encoders. <br>
`Proj_Setup.h` and `Proj_Setup.cpp` contain the rest of the functions for the current project. 
`esp32s3_control_new` contains the setup of the motor and event loops

This is the DC motor class. This class contains all the properties being used by a motor. 
```cpp
class DCMotor{
private:
  int mt_D1;          // direction control one
  int mt_D2;          // direction control two
  int ledc_channel;   // pwm channel for the motor
  int mt_resol;       // pwm resolution
  int mt_freq;        // pwm frequency
  int max_pwm;        // max pwm value

public:
    
  // for motor speed sensing
  volatile long motor_pulse_count = 0;

  int mt_HALL_A; // hall sensor phase A port
  int mt_HALL_B; // hall sensor phase B port

  // constructor and destructor
  DCMotor();
  DCMotor(int D1, int D2, int PWM, int HALL_A, int HALL_B, int channel, int freq, int resol);
  ~DCMotor();

  // member functions
  void setUpMotor();
  void motorCtrl(int pwmInput);
};
```
`motor_pulse_count`, `mt_HALL_A`, and `mt_HALL_B` are marked as public for convenience. Because other codes need to use them to perform speed computations and capture current speed.

ESP32S3 does not have a CAN bus. The simplest solution is to use interrupt approaches. The [previous part](#mcu-code-begin) has all information on computing the speed and direction based on the readings from the hall encoder. In the original implementation, the interrupt setup for the motors is also in the class. However, the Arduino IDE has some weird issues with it. I move that part to `Proj_setup.cpp`

```cpp
void IRAM_ATTR motorOneIRQ(){ 
    if(digitalRead(Motor_one.mt_HALL_A)){
        Motor_one.motor_pulse_count++;
    }
    else{
        Motor_one.motor_pulse_count--;
    }
}

void IRAM_ATTR motorTwoIRQ(){
    if(digitalRead(Motor_two.mt_HALL_A)){
        Motor_two.motor_pulse_count++;
    }
    else{
        Motor_two.motor_pulse_count--;
    }
}

void setupMotorInterrupt(){
    attachInterrupt(digitalPinToInterrupt(Motor_one.mt_HALL_B), motorOneIRQ, RISING);
    attachInterrupt(digitalPinToInterrupt(Motor_two.mt_HALL_B), motorTwoIRQ, RISING);
}
```
`attachInterrupt` and `digitalPinToInterrupt` are functions from Arduino IDE that set up the external interrupts on the GPIOs of an MCU. The `IRAM_ATTR` is featured in ESP32S3. Functions with `IRAM_ATTR` will be stored in memory. In the project, interrupts are called frequently. Putting the interrupt service handler on RAM can optimize performance. The function accessing time will be shorter.

Object declarations
```cpp
DCMotor Motor_one(MT1_D1, MT1_D2, MT1_PWM, MT1_HALL_A, MT1_HALL_B, CHAN_MT_ONE, MT_FREQ, RESOL);
DCMotor Motor_two(MT2_D1, MT2_D2, MT2_PWM, MT2_HALL_A, MT2_HALL_B, CHAN_MT_TWO, MT_FREQ, RESOL);
```

I wrote two versions of the speed control. The first version was a naive PID implementation. It worked, but it was not robust. I am not an expert in control theory. I create the second version of the motor speed control using [QuickPID](https://github.com/Dlloydev/QuickPID). It has anti-windup and other special features to optimize the PID calculation.

Creating PID objects
```cpp
QuickPID MT1_PID(&actualSpeed_one, &output_one, &targetSpeed_one);
QuickPID MT2_PID(&actualSpeed_two, &output_two, &targetSpeed_two);
```
Setting up the PID
```cpp
void QuickPID_Init(){
    MT1_PID.Reset();
    MT1_PID.SetTunings(Kp_one, Ki_one, Kd_one);
    MT1_PID.SetSampleTimeUs(pid_interval * 1000);
    MT1_PID.SetMode(MT1_PID.Control::automatic);
    MT1_PID.SetOutputLimits((float)(MAX_PWM) * (-1), (float)(MAX_PWM));

    MT2_PID.Reset();
    MT2_PID.SetTunings(Kp_two, Ki_two, Kd_two);
    MT2_PID.SetSampleTimeUs(pid_interval * 1000);
    MT2_PID.SetMode(MT2_PID.Control::automatic);
    MT2_PID.SetOutputLimits((float)(MAX_PWM) * (-1), (float)(MAX_PWM));
}
```
PID sampling and computation
```cpp
void QuickPID_Compute(){
    // this mind need to fixed later, it is ok for now, but not sure
    noInterrupts();
    if(millis() - pid_compute_time >= pid_interval){
        // compute motor two speed, unit = revolutions per min
        prevSpeed_two = (actualSpeed_two > 1 || actualSpeed_two < -1) ? actualSpeed_two : prevSpeed_two;
        actualSpeed_two = (float)(Motor_two.motor_pulse_count) * speed_constant ;
        // Motor_two.motor_pulse_count = 0; 

        // compute motor one speed, unit = revolutions per min
        prevSpeed_one = (actualSpeed_one > 1 || actualSpeed_one < -1) ? actualSpeed_one : prevSpeed_one;
        actualSpeed_one = (float)(Motor_one.motor_pulse_count) * speed_constant;
        
        // Motor_one.motor_pulse_count = 0;
        MT1_PID.Compute();
        MT2_PID.Compute();

        Motor_one.motorCtrl((int)(round(output_one)));
        Motor_two.motorCtrl((int)(round(output_two)));
        // noInterrupts();

        Motor_two.motor_pulse_count = 0; 
        Motor_one.motor_pulse_count = 0;
        pid_compute_time = millis();
    }
    interrupts();
}
```
There are some other small details that I need to pay attention to, but those 3 pieces of the code are the core of the motor speed control.

Linear acutactor does not have its own class because it is simple enough. It has three parts: setup, motor control, and state machine.
```cpp
void setupLinearActuator(){
    pinMode(Ln_Act_D1, OUTPUT);
    pinMode(Ln_Act_D2, OUTPUT);
    ledcSetup(CHAN_LN_ACT, LA_FREQ, RESOL);
    ledcAttachPin(Ln_Act_PWM, CHAN_LN_ACT);
    
    lid.lidState = CLOSE;
    lid.shouldOpen = true;
    lid.currentTime = 0;
}

void linearActCtrl(int pwmInputLnAct){
    if(pwmInputLnAct == 0){ // motor not moving
        digitalWrite(Ln_Act_D1, LOW);
        digitalWrite(Ln_Act_D2, LOW);
        return;
    }
    
    if(pwmInputLnAct > 0){ // forward movement
        digitalWrite(Ln_Act_D1, HIGH);
        digitalWrite(Ln_Act_D2, LOW);
        ledcWrite(CHAN_LN_ACT, constrain(pwmInputLnAct, 0, MAX_PWM));
    }
    else{ // backward movement
        digitalWrite(Ln_Act_D1, LOW);
        digitalWrite(Ln_Act_D2, HIGH);
        ledcWrite(CHAN_LN_ACT, -constrain(pwmInputLnAct, -MAX_PWM, 0));
    }
}

lidStateEnum checkLid(){
    switch(lid.lidState){
        case OPEN:
            openLid = false;
            lid.shouldOpen = false;
            if(millis() - lid.currentTime > LID_TIME){ // if open is long enough
                lid.lidState = TRANS;
                lid.currentTime = millis();
            }
            break;
        case TRANS:
            openLid = false;
            if(millis() - lid.currentTime <= LID_TRANS_TIME){ // we can make trans time longer
                if(lid.shouldOpen){ // determine if is open or closing
                    linearActCtrl(-200);
                }
                else{
                    linearActCtrl(200);
                }
            }
            else{
                linearActCtrl(0); 
                lid.currentTime = millis();
                if(lid.shouldOpen){
                    lid.lidState = OPEN;
                }
                else{
                    lid.lidState = CLOSE;
                }
            }
            break;
        case CLOSE: // lid is in close state
            lid.currentTime = millis();
            lid.shouldOpen = true;
            lid.lidState = CLOSE;
            if(openLid){
                lid.lidState = TRANS;
            }
            break;
        default:
            break;
    }
    return lid.lidState;
}
```
The `checkLid()` function is built based on the state machine based on the diagram



The `enum` and `struct` used in the linear actuator logic:
```cpp
/* trashbin state info */
enum lidStateEnum {OPEN=0, TRANS=1, CLOSE=2};	// trash bin lid states

/* linear actuator control info */
typedef struct LinearActInfo{
    lidStateEnum lidState;
    bool shouldOpen;
    unsigned long currentTime;
} LinearActInfo;
```
The purpose of this structure is to keep track of useful state information.

Based on our design, I changed `LID_TIME` to 30000 ms (30 s). To ensure the linear can fully open and close, I set the transition time `LID_TRANS_TIME` to 10000 ms (10 s). The lid operation (close -> open -> close) takes about 50 seconds in total.

## March 26, 2024 
### Debug Customized PCB: Unable to Upload code to MCU with USB-to-UART

The customized PCB's auto program circuit (UART circuit) is correct. the MCU could not be programmed because I connected the TX/RX on the UART bridge to the wrong ports on the MCU UART. 

The correct connection when programming with USB-to-UART:
- USB-to-UART bridge TX <---> MCU RX
- USB-to-UART bridge RX <---> MCU TX

`RTS` and `DTR` pins must be connected to ensure that the serial communication between the MCU and the laptop. For debugging purpose, I used the serial monitor in Arduino IDE to verify that the MCU is communicating with the PC/laptop.

**TODO:**
- Debug Mirco-USB programming for MCU. MCU still cannot communicate/program via Micro-USB

## March 29 to March 31, 2024
### MCU Code: Motor Control - PID tunning

The motor control need to react quickly to the change in the set point (target) and generate a smooth transition from one speed to another. 

I do not know how to dynamically tuning my PID, so I just use the classic method: trial and error.

Motor model: 12V JGB37-520 178 RPM <br>
Hall Encoder PPR: 11 <br>
Reduction Ratio: 56 <br>
PID sample interval: 100ms

The testing script `pid_analysis.ipynb` can be found in `debugging` directory. The trial data (in `csv` format) can be found in `debugging/pid_data` directory.

The order of tuning parameters: P -> D -> I<br>
Below ared some results with different P, D, I

$P = 1.1$

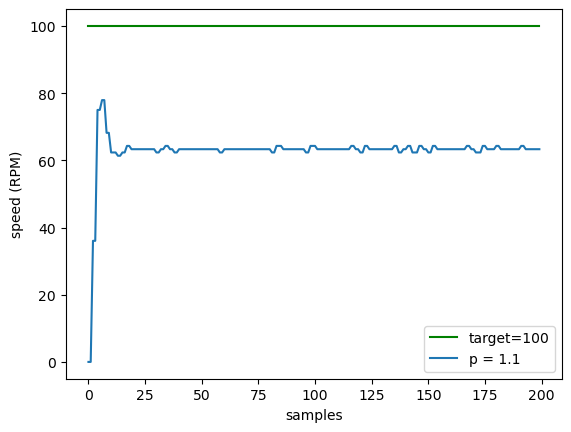
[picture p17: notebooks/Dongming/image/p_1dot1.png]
PID graph for p = 1.1


$P = 1.25$

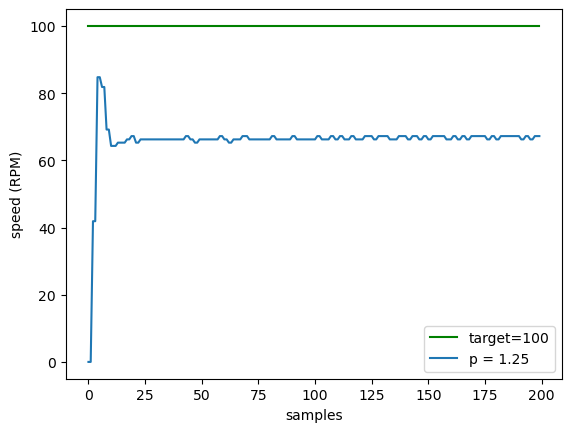
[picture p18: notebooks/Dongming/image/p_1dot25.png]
PID graph for p = 1.25


Increase P to reach some sort of damping <br>
$P = 2.3, D=0.0001$

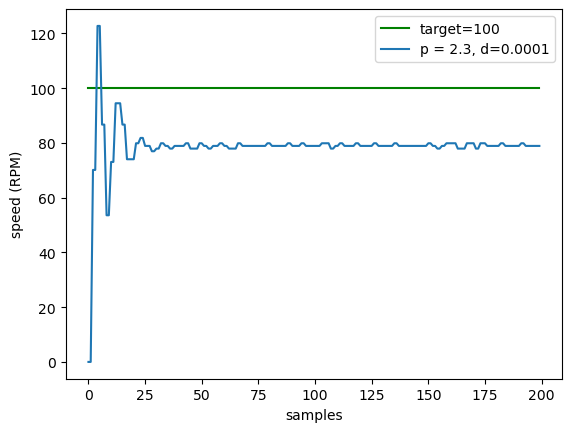
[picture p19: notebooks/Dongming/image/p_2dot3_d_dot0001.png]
PID graph for p = 2.3, d=0.0001


Tuning based on $P = 2.3, D=0.0001$ <br> 
$P = 2.3, D = 0.05$

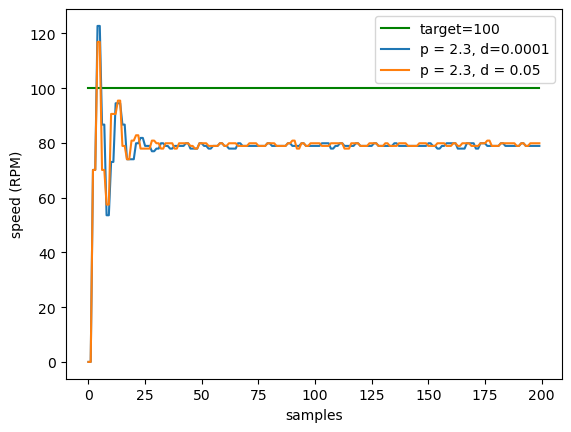
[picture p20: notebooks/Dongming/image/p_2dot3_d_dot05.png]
PID graph for p = 2.3, d=0.05


$P = 2.3, D = 0.075$

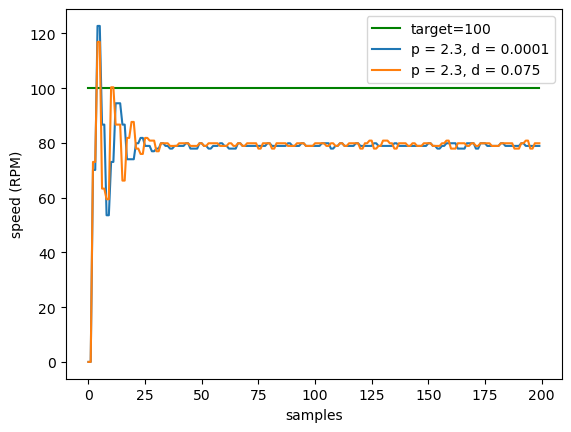
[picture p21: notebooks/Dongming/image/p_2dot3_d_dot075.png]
PID graph for p = 2.3, d=0.075


$P = 2.3, D = 0.125$

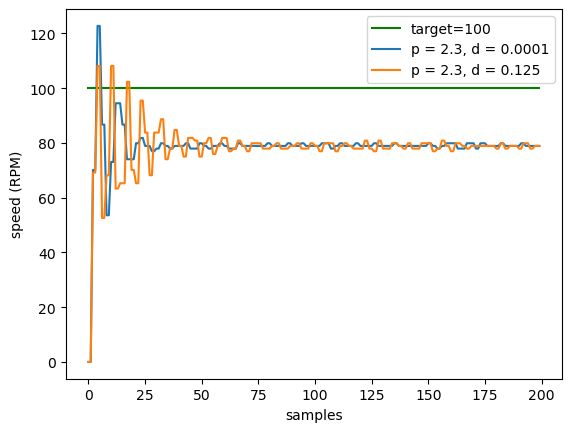
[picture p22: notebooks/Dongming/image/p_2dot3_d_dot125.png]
PID graph for p = 2.3, d=0.125


$P = 2.3, D = 0.1$

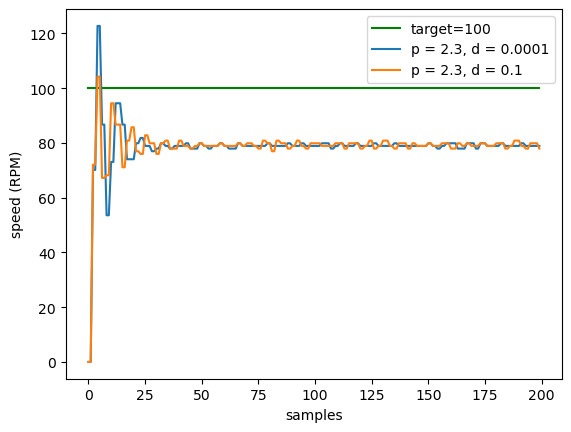
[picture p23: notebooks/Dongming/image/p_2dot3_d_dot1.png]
PID graph for p = 2.3, d=0.1


The P might be aggressive, reducing P to 1.15 <br>
$P = 1.15, D = 0.1$

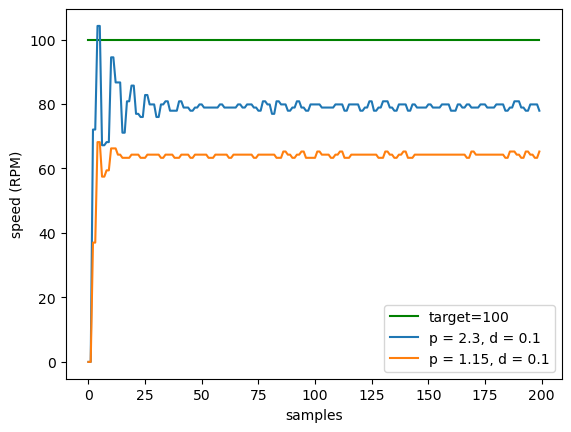
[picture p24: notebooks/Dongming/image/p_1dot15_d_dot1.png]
PID graph for p = 1.5, d=0.1


Using $P = 1.15, D = 0.1$ as a reference and comparing the differences

$P = 1.15, D = 0.15$

PID graph for p = 1.5, d=0.15

$P = 1.15, D = 0.11$

PID graph for p = 1.5, d=0.11

$P = 1.15, D = 0.105$

PID graph for p = 1.5, d=0.105

$P = 1.15, D = 0.08$

PID graph for p = 1.5, d=0.08

With $P \geq 1$, the resulting curve will always have a sudden jump at the beginning. When $P \lt 1$, the sudden jump at the beginning becomes less. The sweet spot of P is around 0.8. The P can quickly respond to errors without creating a sudden jump at the beginning. With $P \approx 0.8$, the D should be around 0.04 to smooth out the sudden jump.

Then, for I, a good one is between 4 and 8. It can quickly lift the PID output to the setpoint. With a greater I and anti-windup, the PID responds faster.

The finalized PID curve with $P=0.8, I=4, D=0.041$

final pid graph

Although the left and right motors might not be the same, but these set of PID parameters can produce similar outputs

left and right motor PID graph

At this point, the PID tuning is completed. Although the PID is tuned based on the 178 RPM motor, it works well on our 60 RPM motor. The probable reason is that the two motors are the same model but with different gear ratios.

**TODO:**
- Step down setpoint when motors cannot meet the setpoint due to various reasons

## April 05, 2024
### PCB Testing: PCB v1

Tested the first version of the customized PCB.

Checklist of working components
- [x] ESP32S3 chip 
- [x] UART code uploading
- [x] reset and boot button (boot button is fried due to soldering, needs to be replaced)  
- [x] power subsystem
- [x] motor one port of the motor driver
- [ ] motor two port of the motor driver
- [x] linear actuator motor driver  
- [ ] Micro-USB communicates with ESP32S3 module 

Motor driver port 2 does not output power to the motor even though the MCU is sending PWM and H-bridge control signals.

## April 08, 2024
### PCB Testing: PCB v1 motor driver port two

Continued testing the first version of the customized PCB with Josh, my EE teammate 

We successfully debugged the issue with motor two port of the motor driver. We found out that the B-sense pin of L298 was not grounded. Because of this, the motor driver outputed 12V to both the positive and negative ports of the motor. The version 1 of the PCB did not have any connection from B-sense to ground, so we solder a jumper from B-sense to the ground of the L298 chip. 

We also tried to debug the micro-usb communication, but we couldn't find enough information to help us debugging this. The pin connections are correct. The Arduino IDE settings are adjusted accordingly. However, neither of our laptops recognizes the USB connection with ESP32S3. 

Checklist of working components
- [x] ESP32S3 chip 
- [x] UART code uploading
- [x] reset and boot button (boot button is fried due to soldering, needs to be replaced)  
- [x] power subsystem
- [x] motor one port of the motor driver
- [x] motor two port of the motor driver
- [x] linear actuator motor driver  
- [ ] Micro-USB communicates with ESP32S3 module (do not know what is going, very unfortunate)

### Project Design: Minor Update on Physical Design

We asked the machine shop to drill a couple of holes in the battery box. We now can pass the power wires from the side and motor wires from the bottom of the base to our PCB, which will sit on top of the battery box. 

For micro-USB communication, all the connections are fine. However, the laptops cannot recognize the USB driver on the ESP32S3. Maybe there are some specific settings we need to pay attention to.

The Plan for project design:
- Get a 3D printed box for the PCB (for hiding wires)

The Plan for project testing:
- Assemble everything
- Run the web service control and motor driver control at the same time
- Make necessary adjustments

## April 10, 2024
### Project Production: Assembling and Testing

Josh and I assembled all parts of the trash bin system.

Checklist for assembling:
- [x] Battery is locked in the battery box 
- [ ] Battery is fixed at a position (may use some dual lock fasteners)
- [x] All wires are connected to the PCB (except the power)
- [ ] 3D printed / cardboard box for PCB 
- [ ] Wire coverage
- [ ] Wire connection re-arrangement
  
We also verified the functionalities of the trash bin system. The ESP32S3 on our PCB can connect to the wifi network successfully. It can receive and quickly process requests from other devices.

## April 12, 2024
### Project Production: Assembling Checklist

Checklist for assembling:
- [ ] Battery is fixed at a position (may use some dual lock fasteners)
- [x] All wires are connected to the PCB (except the power)
- [ ] 3D printed / cardboard box for PCB 
- [x] Wire coverage (most of the wires are being covered)
- [x] Wire connection re-arrangement

## April 17, 2024
### Project Production: Product Testing without Raspberry Pi

Both of our motors are strong enough to move the entire bin. 

We have measured the speed and time for turning the bin 90 degrees.

Unfortunately, the Raspberry Pi was accidentally shut down while we were doing other tests. The HDMI port of the monitor cannot recognize the video signals from Pi. We were not sure if the Pi was damaged. We have three more Pi's ready to use.

## April 18, 2024
### Project Production: 3D Printed Box
I finished making the 3D printed box for our PCB. It fits perfectly. Now we just need to wait for the fasteners arrived.

The interior:

the inside look of the 3D-printed PCB box

<br>

With lid:

the 3D-printed PCB box with lid

Remaining tests: Raspberry Pi remote control and path planning.

## April 19, 2024
### Project Production: Intergration Testing Part 1

Checklist for assembling:
- [x] Battery is fixed at a position (may use some dual lock fasteners)
- [x] All wires are connected to the PCB (except the power)
- [x] 3D printed / cardboard box for PCB 
- [x] Wire coverage (most of the wires are being covered)
- [x] Wire connection re-arrangement

One Raspberry Pi was broken in a sudden. To the best of our knowledge, nothing shorten the Raspberry Pi. The cause of this is unkown. So we ended up using one of our backup Raspberry Pi (Model: 4B, RAM: 4GB).

Remaining Raspberry Pi: Raspberry Pi 4B 2GB

We tested the map formation, path planning, and hand gestures without remotely controlling the bin. Everything seemed to be fine so far. 

## April 20, 2024
### Project Production: Intergration Testing Part 2

We tested the map formation, path planning, and hand gestures while remotely controlling the bin. We discovered that the bin can easily go off the track and does not follow the path timely.

We adjusted the PID parameter to make the bin to be more responsive. <br>
P = 0.8, I = 16, D = 0.041

The integral can lift the outputs to the desired target much faster. 

We also increased the wait time on the CV end to allow the MCU sufficient time to process the incoming data and turn the motors.

## April 21, 2024
### Project Production: Demo Setup
We set up the environment for our project demoing.

The bin:

ready to serve trashb bin, the bin image

The Pi:

ready to serve trashb bin, the pi image

We also did some testing on the CV code and remote control. Everything worked fine. The bin may skip one command due to network conditions and insufficient wait time on the computer vision side, but this is within our tolerance.

**What a journey! The project Ready-To-Serve Trash Bin is finished!** 

***Demo Time: 10:30:00 AM, April 22, 2024***

## EXTRA NOTE
Note: the commit history might not be the same as the timeline here... the dev log might be earlier or later than the commit history. But they are almost aligned.

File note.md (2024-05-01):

# PCB updates note

[Update]: ESP32-S3 MCU control circuit version 2
- Made pin assignment for motor connnections 
- Each DC motor uses 5 pins (Motor Hall Phase A & B, Motor direction control port A & B, PWM pin)
- Linear Actuator uses 3 pins (PWM pin, direcetion control pin)
- Added testing output pins for the MCU control circuit (for motors specifically)
- Reduced the numbers of ports for other programmable GPIOs
- The output pins are Connector_Pinhead (male pins)

[Update]: Update filenames and add a quick note
- `esp32s3-chip-only-sch-v1.zip`: ESP32S3 minimal schematic configuration (the basic layout for the chip to work )
- `power-and-motors-pcb-v1.zip`: power circuit and motor driver pcb schematic and layout
- `ready-to-serve-trash-bin-v0.zip`: the basic version of the PCB
- `ready-to-serve-trash-bin-v1.zip`: the current version of the PCB and schematic, physical PCB and components are ready for testing 
- `ready-to-serve-trash-bin-v2.zip`: the new PCB layout, same schematics but different arrangement of components on the PCB (by Josh)
- `ready-to-serve-trash-bin-v3.zip`: the final version with small buttons (by Josh)
- `ready-to-serve-trash-bin-v4.zip`: the final version with big buttons (by Josh)

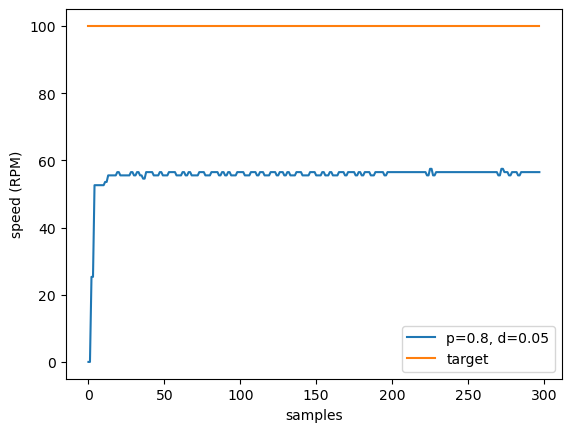
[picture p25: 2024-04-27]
notebooks/Dongming/image/p_dot8_d_dot05.png

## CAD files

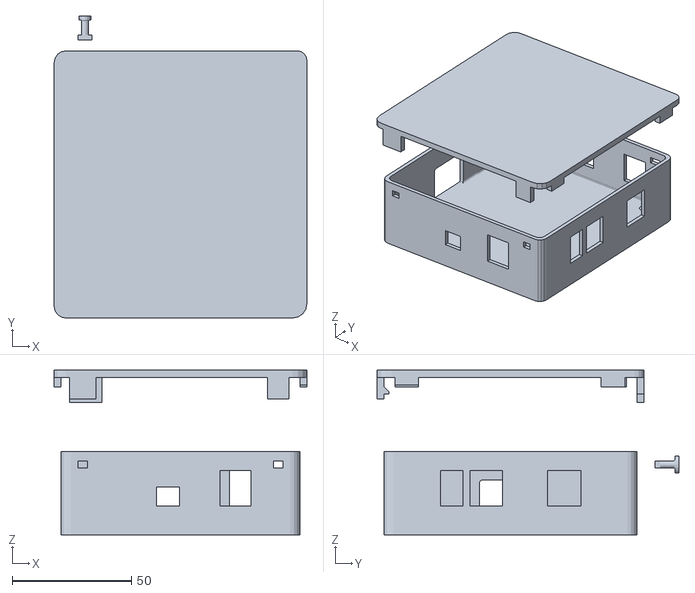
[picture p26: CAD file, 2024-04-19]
3D_Model_PCB_Box/STLs/445_full_view_v2_above.stl
106.0 x 126.6 x 69.0

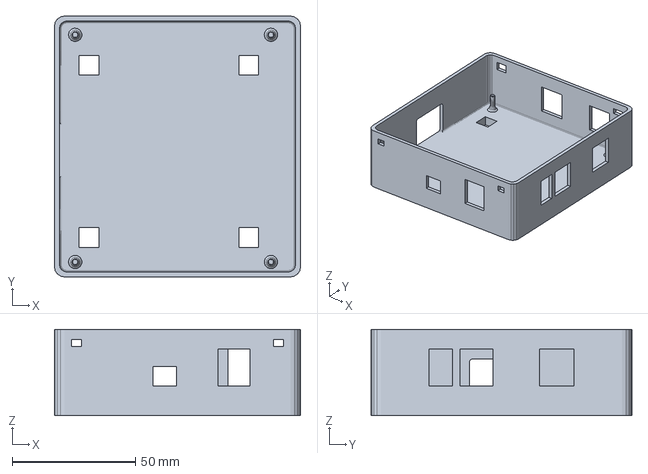
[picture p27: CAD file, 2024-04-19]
3D_Model_PCB_Box/445_box_circuit_v3_new.3mf
100.0 x 106.0 x 35.0 mm

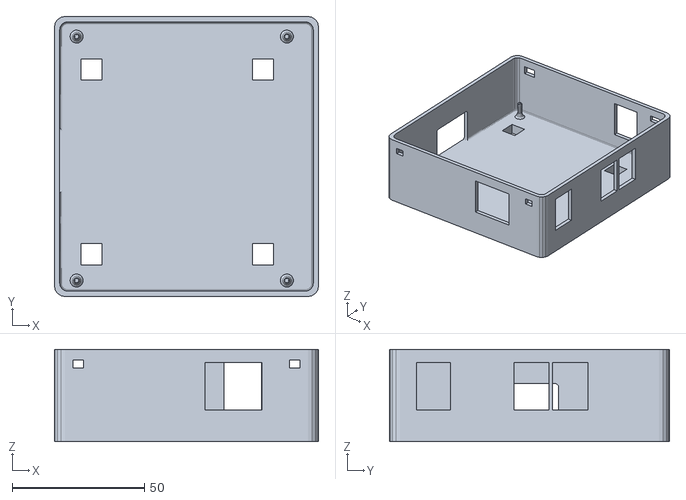
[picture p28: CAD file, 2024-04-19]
3D_Model_PCB_Box/STLs/445_box_v1.stl
100.0 x 106.0 x 35.0

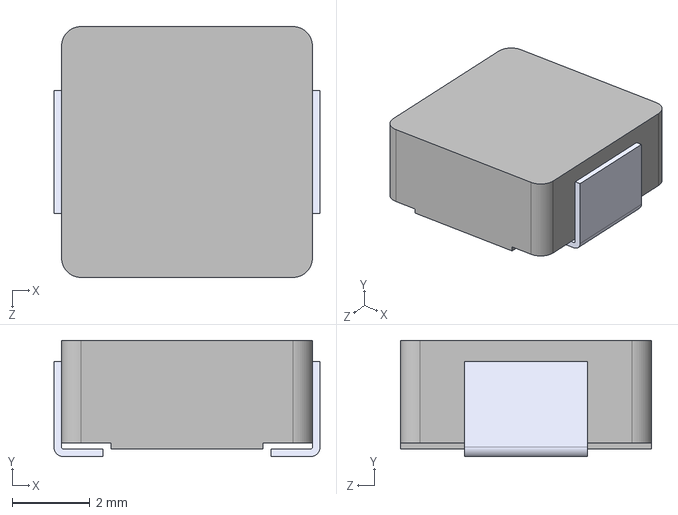
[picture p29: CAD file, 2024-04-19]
extra_component/IHLP2525CZER4R7M01.STEP
6.86 x 3.00 x 6.47 mm

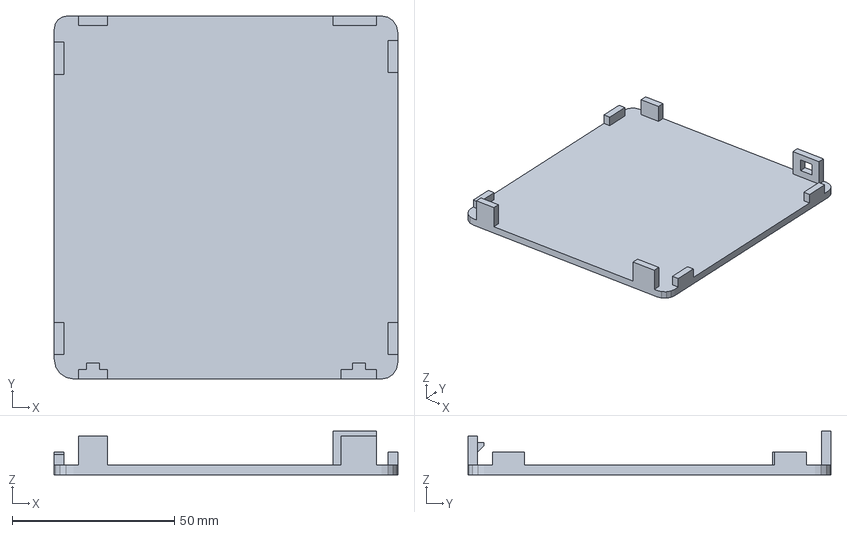
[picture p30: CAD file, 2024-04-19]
3D_Model_PCB_Box/445_lid_model.3mf
106.0 x 112.0 x 13.5 mm

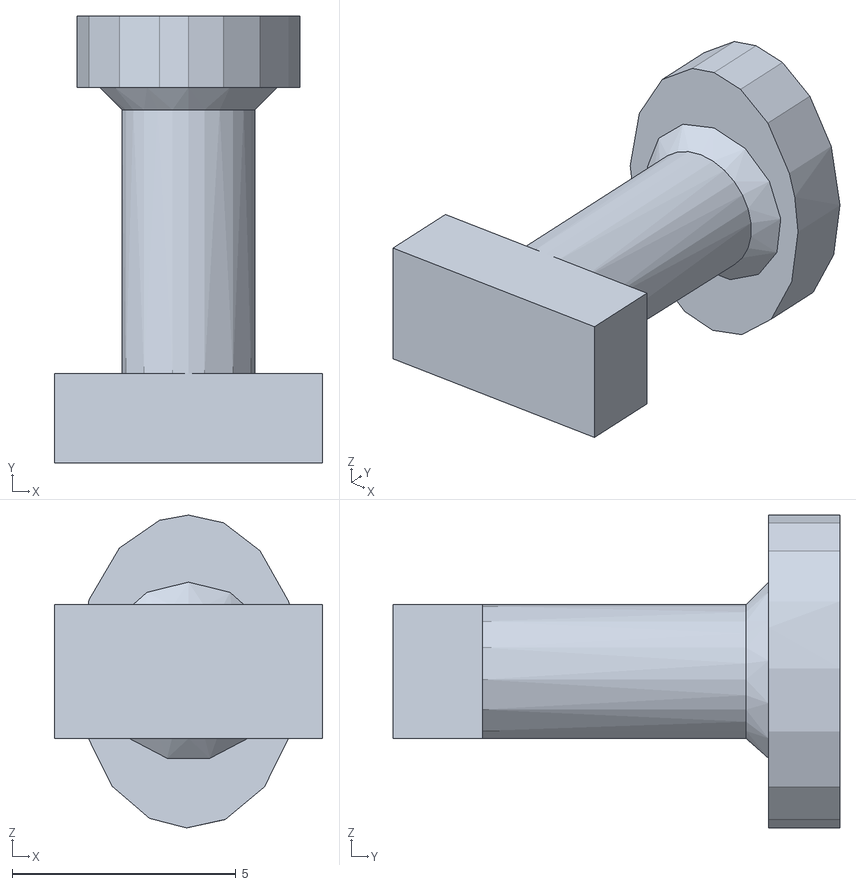
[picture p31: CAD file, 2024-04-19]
3D_Model_PCB_Box/STLs/445_tiny_lock.stl
6.00 x 10.0 x 7.00

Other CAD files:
3D_Model_PCB_Box/STLs/445_lid_v2_above_circuit.stl
3D_Model_PCB_Box/STLs/445_box_v2_above_circuit.stl
3D_Model_PCB_Box/445_box_circuit_v1_new.3mf

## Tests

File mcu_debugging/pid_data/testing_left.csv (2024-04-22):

output_one:72.00 | Detected_one:0.00 | Target_one:30.00
output_one:72.00 | Detected_one:0.00 | Target_one:30.00
output_one:72.00 | Detected_one:0.00 | Target_one:30.00
output_one:106.40 | Detected_one:4.84 | Target_one:30.00
output_one:106.40 | Detected_one:4.84 | Target_one:30.00
output_one:117.80 | Detected_one:15.81 | Target_one:30.00
output_one:117.80 | Detected_one:15.81 | Target_one:30.00
output_one:119.60 | Detected_one:24.85 | Target_one:30.00
output_one:119.60 | Detected_one:24.85 | Target_one:30.00
output_one:113.40 | Detected_one:31.31 | Target_one:30.00
output_one:113.40 | Detected_one:31.31 | Target_one:30.00
output_one:113.40 | Detected_one:31.31 | Target_one:30.00
output_one:104.89 | Detected_one:34.53 | Target_one:30.00
output_one:104.89 | Detected_one:34.53 | Target_one:30.00
output_one:95.33 | Detected_one:35.83 | Target_one:30.00
output_one:95.33 | Detected_one:35.83 | Target_one:30.00
output_one:85.63 | Detected_one:36.15 | Target_one:30.00
output_one:85.63 | Detected_one:36.15 | Target_one:30.00
output_one:76.83 | Detected_one:35.83 | Target_one:30.00
output_one:76.83 | Detected_one:35.83 | Target_one:30.00
output_one:70.10 | Detected_one:34.86 | Target_one:30.00
output_one:70.10 | Detected_one:34.86 | Target_one:30.00
output_one:66.46 | Detected_one:33.24 | Target_one:30.00
output_one:66.46 | Detected_one:33.24 | Target_one:30.00
output_one:66.46 | Detected_one:33.24 | Target_one:30.00
output_one:63.33 | Detected_one:32.28 | Target_one:30.00
output_one:63.33 | Detected_one:32.28 | Target_one:30.00
output_one:62.92 | Detected_one:30.98 | Target_one:30.00
output_one:62.92 | Detected_one:30.98 | Target_one:30.00
output_one:64.45 | Detected_one:29.69 | Target_one:30.00
output_one:64.45 | Detected_one:29.69 | Target_one:30.00
output_one:65.32 | Detected_one:29.37 | Target_one:30.00
output_one:65.32 | Detected_one:29.37 | Target_one:30.00
output_one:68.91 | Detected_one:28.40 | Target_one:30.00
output_one:68.91 | Detected_one:28.40 | Target_one:30.00
output_one:68.91 | Detected_one:28.40 | Target_one:30.00
output_one:69.26 | Detected_one:29.05 | Target_one:30.00
output_one:69.26 | Detected_one:29.05 | Target_one:30.00
output_one:71.04 | Detected_one:29.05 | Target_one:30.00
output_one:71.04 | Detected_one:29.05 | Target_one:30.00
output_one:71.66 | Detected_one:29.37 | Target_one:30.00
output_one:71.66 | Detected_one:29.37 | Target_one:30.00
output_one:71.89 | Detected_one:29.69 | Target_one:30.00
output_one:71.89 | Detected_one:29.69 | Target_one:30.00
output_one:72.52 | Detected_one:29.69 | Target_one:30.00
output_one:72.52 | Detected_one:29.69 | Target_one:30.00
output_one:72.52 | Detected_one:29.69 | Target_one:30.00
output_one:72.10 | Detected_one:30.02 | Target_one:30.00
output_one:72.10 | Detected_one:30.02 | Target_one:30.00
output_one:73.11 | Detected_one:29.69 | Target_one:30.00
output_one:73.11 | Detected_one:29.69 | Target_one:30.00
output_one:73.47 | Detected_one:29.69 | Target_one:30.00
output_one:73.47 | Detected_one:29.69 | Target_one:30.00
output_one:74.87 | Detected_one:29.37 | Target_one:30.00
output_one:74.87 | Detected_one:29.37 | Target_one:30.00
output_one:74.84 | Detected_one:29.69 | Target_one:30.00
output_one:74.84 | Detected_one:29.69 | Target_one:30.00
output_one:75.46 | Detected_one:29.69 | Target_one:30.00
output_one:75.46 | Detected_one:29.69 | Target_one:30.00
output_one:75.46 | Detected_one:29.69 | Target_one:30.00
output_one:74.14 | Detected_one:30.34 | Target_one:30.00
output_one:74.14 | Detected_one:30.34 | Target_one:30.00
output_one:73.86 | Detected_one:30.34 | Target_one:30.00
output_one:73.86 | Detected_one:30.34 | Target_one:30.00
output_one:73.32 | Detected_one:30.34 | Target_one:30.00
output_one:73.32 | Detected_one:30.34 | Target_one:30.00
output_one:71.87 | Detected_one:30.66 | Target_one:30.00
output_one:71.87 | Detected_one:30.66 | Target_one:30.00
output_one:71.85 | Detected_one:30.34 | Target_one:30.00
output_one:71.85 | Detected_one:30.34 | Target_one:30.00
output_one:71.85 | Detected_one:30.34 | Target_one:30.00
output_one:70.27 | Detected_one:30.66 | Target_one:30.00
output_one:70.27 | Detected_one:30.66 | Target_one:30.00
output_one:70.25 | Detected_one:30.34 | Target_one:30.00
output_one:70.25 | Detected_one:30.34 | Target_one:30.00
output_one:70.48 | Detected_one:30.02 | Target_one:30.00
output_one:70.48 | Detected_one:30.02 | Target_one:30.00
output_one:70.32 | Detected_one:30.02 | Target_one:30.00
output_one:70.32 | Detected_one:30.02 | Target_one:30.00
output_one:69.39 | Detected_one:30.34 | Target_one:30.00
output_one:69.39 | Detected_one:30.34 | Target_one:30.00
output_one:70.79 | Detected_one:29.69 | Target_one:30.00
output_one:70.79 | Detected_one:29.69 | Target_one:30.00
output_one:70.79 | Detected_one:29.69 | Target_one:30.00
output_one:69.20 | Detected_one:30.34 | Target_one:30.00
output_one:69.20 | Detected_one:30.34 | Target_one:30.00
output_one:70.74 | Detected_one:29.69 | Target_one:30.00
output_one:70.74 | Detected_one:29.69 | Target_one:30.00
output_one:70.06 | Detected_one:30.02 | Target_one:30.00
output_one:70.06 | Detected_one:30.02 | Target_one:30.00
output_one:71.07 | Detected_one:29.69 | Target_one:30.00
output_one:71.07 | Detected_one:29.69 | Target_one:30.00
output_one:72.34 | Detected_one:29.37 | Target_one:30.00
output_one:72.34 | Detected_one:29.37 | Target_one:30.00
output_one:72.34 | Detected_one:29.37 | Target_one:30.00
output_one:73.21 | Detected_one:29.37 | Target_one:30.00
output_one:73.21 | Detected_one:29.37 | Target_one:30.00
output_one:74.22 | Detected_one:29.37 | Target_one:30.00
output_one:74.22 | Detected_one:29.37 | Target_one:30.00
output_one:74.32 | Detected_one:29.69 | Target_one:30.00
output_one:74.32 | Detected_one:29.69 | Target_one:30.00
output_one:74.94 | Detected_one:29.69 | Target_one:30.00
output_one:74.94 | Detected_one:29.69 | Target_one:30.00
output_one:73.62 | Detected_one:30.34 | Target_one:30.00
output_one:73.62 | Detected_one:30.34 | Target_one:30.00
output_one:73.62 | Detected_one:30.34 | Target_one:30.00
output_one:73.34 | Detected_one:30.34 | Target_one:30.00
output_one:73.34 | Detected_one:30.34 | Target_one:30.00
output_one:71.89 | Detected_one:30.66 | Target_one:30.00
output_one:71.89 | Detected_one:30.66 | Target_one:30.00
output_one:70.97 | Detected_one:30.66 | Target_one:30.00
output_one:70.97 | Detected_one:30.66 | Target_one:30.00
output_one:69.91 | Detected_one:30.66 | Target_one:30.00
output_one:69.91 | Detected_one:30.66 | Target_one:30.00
output_one:69.76 | Detected_one:30.34 | Target_one:30.00
output_one:69.76 | Detected_one:30.34 | Target_one:30.00
output_one:69.08 | Detected_one:30.34 | Target_one:30.00
output_one:69.08 | Detected_one:30.34 | Target_one:30.00
output_one:69.08 | Detected_one:30.34 | Target_one:30.00
output_one:68.54 | Detected_one:30.34 | Target_one:30.00
output_one:68.54 | Detected_one:30.34 | Target_one:30.00
output_one:68.90 | Detected_one:30.02 | Target_one:30.00
output_one:68.90 | Detected_one:30.02 | Target_one:30.00
output_one:68.75 | Detected_one:30.02 | Target_one:30.00
output_one:68.75 | Detected_one:30.02 | Target_one:30.00
output_one:68.72 | Detected_one:30.02 | Target_one:30.00
output_one:68.72 | Detected_one:30.02 | Target_one:30.00
output_one:68.69 | Detected_one:30.02 | Target_one:30.00
output_one:68.69 | Detected_one:30.02 | Target_one:30.00
output_one:68.69 | Detected_one:30.02 | Target_one:30.00
output_one:68.67 | Detected_one:30.02 | Target_one:30.00
output_one:68.67 | Detected_one:30.02 | Target_one:30.00
output_one:69.55 | Detected_one:29.69 | Target_one:30.00
output_one:69.55 | Detected_one:29.69 | Target_one:30.00
output_one:70.82 | Detected_one:29.37 | Target_one:30.00
output_one:70.82 | Detected_one:29.37 | Target_one:30.00
output_one:70.78 | Detected_one:29.69 | Target_one:30.00
output_one:70.78 | Detected_one:29.69 | Target_one:30.00
output_one:72.31 | Detected_one:29.37 | Target_one:30.00
output_one:72.31 | Detected_one:29.37 | Target_one:30.00
output_one:74.09 | Detected_one:29.05 | Target_one:30.00
output_one:74.09 | Detected_one:29.05 | Target_one:30.00
output_one:74.09 | Detected_one:29.05 | Target_one:30.00
output_one:74.58 | Detected_one:29.37 | Target_one:30.00
output_one:74.58 | Detected_one:29.37 | Target_one:30.00
output_one:73.90 | Detected_one:30.02 | Target_one:30.00
output_one:73.90 | Detected_one:30.02 | Target_one:30.00
output_one:74.14 | Detected_one:30.02 | Target_one:30.00
output_one:74.14 | Detected_one:30.02 | Target_one:30.00
output_one:72.30 | Detected_one:30.66 | Target_one:30.00
output_one:72.30 | Detected_one:30.66 | Target_one:30.00
output_one:71.51 | Detected_one:30.66 | Target_one:30.00
output_one:71.51 | Detected_one:30.66 | Target_one:30.00
output_one:71.51 | Detected_one:30.66 | Target_one:30.00
output_one:70.45 | Detected_one:30.66 | Target_one:30.00
output_one:70.45 | Detected_one:30.66 | Target_one:30.00
output_one:69.39 | Detected_one:30.66 | Target_one:30.00
output_one:69.39 | Detected_one:30.66 | Target_one:30.00
output_one:69.24 | Detected_one:30.34 | Target_one:30.00
output_one:69.24 | Detected_one:30.34 | Target_one:30.00
output_one:68.57 | Detected_one:30.34 | Target_one:30.00
output_one:68.57 | Detected_one:30.34 | Target_one:30.00
output_one:68.02 | Detected_one:30.34 | Target_one:30.00
output_one:68.02 | Detected_one:30.34 | Target_one:30.00
output_one:68.02 | Detected_one:30.34 | Target_one:30.00
output_one:68.39 | Detected_one:30.02 | Target_one:30.00
output_one:68.39 | Detected_one:30.02 | Target_one:30.00
output_one:68.23 | Detected_one:30.02 | Target_one:30.00
output_one:68.23 | Detected_one:30.02 | Target_one:30.00
output_one:68.20 | Detected_one:30.02 | Target_one:30.00
output_one:68.20 | Detected_one:30.02 | Target_one:30.00
output_one:69.09 | Detected_one:29.69 | Target_one:30.00
output_one:69.09 | Detected_one:29.69 | Target_one:30.00
output_one:69.44 | Detected_one:29.69 | Target_one:30.00
output_one:69.44 | Detected_one:29.69 | Target_one:30.00
output_one:69.93 | Detected_one:29.69 | Target_one:30.00
output_one:69.93 | Detected_one:29.69 | Target_one:30.00
output_one:69.93 | Detected_one:29.69 | Target_one:30.00
output_one:70.42 | Detected_one:29.69 | Target_one:30.00
output_one:70.42 | Detected_one:29.69 | Target_one:30.00
output_one:70.92 | Detected_one:29.69 | Target_one:30.00
output_one:70.92 | Detected_one:29.69 | Target_one:30.00
output_one:73.22 | Detected_one:29.05 | Target_one:30.00
output_one:73.22 | Detected_one:29.05 | Target_one:30.00
output_one:73.57 | Detected_one:29.37 | Target_one:30.00
output_one:73.57 | Detected_one:29.37 | Target_one:30.00
output_one:74.71 | Detected_one:29.37 | Target_one:30.00
output_one:74.71 | Detected_one:29.37 | Target_one:30.00
output_one:74.71 | Detected_one:29.37 | Target_one:30.00
output_one:73.90 | Detected_one:30.02 | Target_one:30.00
output_one:73.90 | Detected_one:30.02 | Target_one:30.00
output_one:72.33 | Detected_one:30.66 | Target_one:30.00
output_one:72.33 | Detected_one:30.66 | Target_one:30.00
output_one:71.54 | Detected_one:30.66 | Target_one:30.00
output_one:71.54 | Detected_one:30.66 | Target_one:30.00
output_one:70.48 | Detected_one:30.66 | Target_one:30.00
output_one:70.48 | Detected_one:30.66 | Target_one:30.00
output_one:69.42 | Detected_one:30.66 | Target_one:30.00
output_one:69.42 | Detected_one:30.66 | Target_one:30.00
output_one:69.27 | Detected_one:30.34 | Target_one:30.00
output_one:69.27 | Detected_one:30.34 | Target_one:30.00
output_one:69.27 | Detected_one:30.34 | Target_one:30.00
output_one:68.59 | Detected_one:30.34 | Target_one:30.00
output_one:68.59 | Detected_one:30.34 | Target_one:30.00
output_one:68.05 | Detected_one:30.34 | Target_one:30.00
output_one:68.05 | Detected_one:30.34 | Target_one:30.00
output_one:67.51 | Detected_one:30.34 | Target_one:30.00
output_one:67.51 | Detected_one:30.34 | Target_one:30.00
output_one:67.87 | Detected_one:30.02 | Target_one:30.00
output_one:67.87 | Detected_one:30.02 | Target_one:30.00
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

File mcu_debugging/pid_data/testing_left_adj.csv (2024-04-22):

output_one:60.00 | Detected_one:0.00 | Target_one:20.00
output_one:60.00 | Detected_one:0.00 | Target_one:20.00
output_one:60.00 | Detected_one:0.00 | Target_one:20.00
output_one:87.93 | Detected_one:3.55 | Target_one:20.00
output_one:87.93 | Detected_one:3.55 | Target_one:20.00
output_one:90.42 | Detected_one:12.91 | Target_one:20.00
output_one:90.42 | Detected_one:12.91 | Target_one:20.00
output_one:82.01 | Detected_one:20.66 | Target_one:20.00
output_one:82.01 | Detected_one:20.66 | Target_one:20.00
output_one:82.01 | Detected_one:20.66 | Target_one:20.00
output_one:66.24 | Detected_one:25.82 | Target_one:20.00
output_one:66.24 | Detected_one:25.82 | Target_one:20.00
output_one:52.28 | Detected_one:27.11 | Target_one:20.00
output_one:52.28 | Detected_one:27.11 | Target_one:20.00
output_one:39.67 | Detected_one:26.79 | Target_one:20.00
output_one:39.67 | Detected_one:26.79 | Target_one:20.00
output_one:32.54 | Detected_one:24.85 | Target_one:20.00
output_one:32.54 | Detected_one:24.85 | Target_one:20.00
output_one:30.84 | Detected_one:22.27 | Target_one:20.00
output_one:30.84 | Detected_one:22.27 | Target_one:20.00
output_one:34.05 | Detected_one:19.69 | Target_one:20.00
output_one:34.05 | Detected_one:19.69 | Target_one:20.00
output_one:34.05 | Detected_one:19.69 | Target_one:20.00
output_one:41.32 | Detected_one:17.43 | Target_one:20.00
output_one:41.32 | Detected_one:17.43 | Target_one:20.00
output_one:47.76 | Detected_one:16.78 | Target_one:20.00
output_one:47.76 | Detected_one:16.78 | Target_one:20.00
output_one:53.93 | Detected_one:16.78 | Target_one:20.00
output_one:53.93 | Detected_one:16.78 | Target_one:20.00
output_one:55.98 | Detected_one:18.07 | Target_one:20.00
output_one:55.98 | Detected_one:18.07 | Target_one:20.00
output_one:57.05 | Detected_one:19.04 | Target_one:20.00
output_one:57.05 | Detected_one:19.04 | Target_one:20.00
output_one:57.05 | Detected_one:19.04 | Target_one:20.00
output_one:53.87 | Detected_one:20.66 | Target_one:20.00
output_one:53.87 | Detected_one:20.66 | Target_one:20.00
output_one:51.01 | Detected_one:21.30 | Target_one:20.00
output_one:51.01 | Detected_one:21.30 | Target_one:20.00
output_one:49.76 | Detected_one:20.98 | Target_one:20.00
output_one:49.76 | Detected_one:20.98 | Target_one:20.00
output_one:47.67 | Detected_one:20.98 | Target_one:20.00
output_one:47.67 | Detected_one:20.98 | Target_one:20.00
output_one:49.00 | Detected_one:20.01 | Target_one:20.00
output_one:49.00 | Detected_one:20.01 | Target_one:20.00
output_one:49.00 | Detected_one:20.01 | Target_one:20.00
output_one:49.69 | Detected_one:19.69 | Target_one:20.00
output_one:49.69 | Detected_one:19.69 | Target_one:20.00
output_one:51.29 | Detected_one:19.37 | Target_one:20.00
output_one:51.29 | Detected_one:19.37 | Target_one:20.00
output_one:53.52 | Detected_one:19.04 | Target_one:20.00
output_one:53.52 | Detected_one:19.04 | Target_one:20.00
output_one:55.31 | Detected_one:19.04 | Target_one:20.00
output_one:55.31 | Detected_one:19.04 | Target_one:20.00
output_one:53.93 | Detected_one:20.01 | Target_one:20.00
output_one:53.93 | Detected_one:20.01 | Target_one:20.00
output_one:53.20 | Detected_one:20.33 | Target_one:20.00
output_one:53.20 | Detected_one:20.33 | Target_one:20.00
output_one:53.20 | Detected_one:20.33 | Target_one:20.00
output_one:51.57 | Detected_one:20.66 | Target_one:20.00
output_one:51.57 | Detected_one:20.66 | Target_one:20.00
output_one:49.28 | Detected_one:20.98 | Target_one:20.00
output_one:49.28 | Detected_one:20.98 | Target_one:20.00
output_one:48.55 | Detected_one:20.66 | Target_one:20.00
output_one:48.55 | Detected_one:20.66 | Target_one:20.00
output_one:47.11 | Detected_one:20.66 | Target_one:20.00
output_one:47.11 | Detected_one:20.66 | Target_one:20.00
output_one:46.90 | Detected_one:20.33 | Target_one:20.00
output_one:46.90 | Detected_one:20.33 | Target_one:20.00
output_one:46.90 | Detected_one:20.33 | Target_one:20.00
output_one:47.20 | Detected_one:20.01 | Target_one:20.00
output_one:47.20 | Detected_one:20.01 | Target_one:20.00
output_one:48.14 | Detected_one:19.69 | Target_one:20.00
output_one:48.14 | Detected_one:19.69 | Target_one:20.00
output_one:48.64 | Detected_one:19.69 | Target_one:20.00
output_one:48.64 | Detected_one:19.69 | Target_one:20.00
output_one:50.36 | Detected_one:19.37 | Target_one:20.00
output_one:50.36 | Detected_one:19.37 | Target_one:20.00
output_one:50.40 | Detected_one:19.69 | Target_one:20.00
output_one:50.40 | Detected_one:19.69 | Target_one:20.00
output_one:50.06 | Detected_one:20.01 | Target_one:20.00
output_one:50.06 | Detected_one:20.01 | Target_one:20.00
output_one:50.06 | Detected_one:20.01 | Target_one:20.00
output_one:50.17 | Detected_one:20.01 | Target_one:20.00
output_one:50.17 | Detected_one:20.01 | Target_one:20.00
output_one:49.05 | Detected_one:20.33 | Target_one:20.00
output_one:49.05 | Detected_one:20.33 | Target_one:20.00
output_one:48.51 | Detected_one:20.33 | Target_one:20.00
output_one:48.51 | Detected_one:20.33 | Target_one:20.00
output_one:47.84 | Detected_one:20.33 | Target_one:20.00
output_one:47.84 | Detected_one:20.33 | Target_one:20.00
output_one:47.18 | Detected_one:20.33 | Target_one:20.00
output_one:47.18 | Detected_one:20.33 | Target_one:20.00
output_one:47.18 | Detected_one:20.33 | Target_one:20.00
output_one:47.61 | Detected_one:20.01 | Target_one:20.00
output_one:47.61 | Detected_one:20.01 | Target_one:20.00
output_one:47.46 | Detected_one:20.01 | Target_one:20.00
output_one:47.46 | Detected_one:20.01 | Target_one:20.00
output_one:48.53 | Detected_one:19.69 | Target_one:20.00
output_one:48.53 | Detected_one:19.69 | Target_one:20.00
output_one:49.03 | Detected_one:19.69 | Target_one:20.00
output_one:49.03 | Detected_one:19.69 | Target_one:20.00
output_one:49.65 | Detected_one:19.69 | Target_one:20.00
output_one:49.65 | Detected_one:19.69 | Target_one:20.00
output_one:49.65 | Detected_one:19.69 | Target_one:20.00
output_one:51.37 | Detected_one:19.37 | Target_one:20.00
output_one:51.37 | Detected_one:19.37 | Target_one:20.00
output_one:51.41 | Detected_one:19.69 | Target_one:20.00
output_one:51.41 | Detected_one:19.69 | Target_one:20.00
output_one:53.27 | Detected_one:19.37 | Target_one:20.00
output_one:53.27 | Detected_one:19.37 | Target_one:20.00
output_one:53.31 | Detected_one:19.69 | Target_one:20.00
output_one:53.31 | Detected_one:19.69 | Target_one:20.00
output_one:54.06 | Detected_one:19.69 | Target_one:20.00
output_one:54.06 | Detected_one:19.69 | Target_one:20.00
output_one:54.69 | Detected_one:19.69 | Target_one:20.00
output_one:54.69 | Detected_one:19.69 | Target_one:20.00
output_one:54.69 | Detected_one:19.69 | Target_one:20.00
output_one:53.11 | Detected_one:20.33 | Target_one:20.00
output_one:53.11 | Detected_one:20.33 | Target_one:20.00
output_one:52.71 | Detected_one:20.33 | Target_one:20.00
output_one:52.71 | Detected_one:20.33 | Target_one:20.00
output_one:50.94 | Detected_one:20.66 | Target_one:20.00
output_one:50.94 | Detected_one:20.66 | Target_one:20.00
output_one:48.66 | Detected_one:20.98 | Target_one:20.00
output_one:48.66 | Detected_one:20.98 | Target_one:20.00
output_one:47.93 | Detected_one:20.66 | Target_one:20.00
output_one:47.93 | Detected_one:20.66 | Target_one:20.00
output_one:47.93 | Detected_one:20.66 | Target_one:20.00
output_one:46.49 | Detected_one:20.66 | Target_one:20.00
output_one:46.49 | Detected_one:20.66 | Target_one:20.00
output_one:47.37 | Detected_one:20.01 | Target_one:20.00
output_one:47.37 | Detected_one:20.01 | Target_one:20.00
output_one:47.09 | Detected_one:20.01 | Target_one:20.00
output_one:47.09 | Detected_one:20.01 | Target_one:20.00
output_one:138.17 | Detected_one:19.69 | Target_one:50.00
output_one:138.17 | Detected_one:19.69 | Target_one:50.00
output_one:177.81 | Detected_one:25.82 | Target_one:50.00
output_one:177.81 | Detected_one:25.82 | Target_one:50.00
output_one:193.51 | Detected_one:36.15 | Target_one:50.00
output_one:193.51 | Detected_one:36.15 | Target_one:50.00
output_one:193.51 | Detected_one:36.15 | Target_one:50.00
output_one:201.20 | Detected_one:43.25 | Target_one:50.00
output_one:201.20 | Detected_one:43.25 | Target_one:50.00
output_one:205.47 | Detected_one:46.80 | Target_one:50.00
output_one:205.47 | Detected_one:46.80 | Target_one:50.00
output_one:206.71 | Detected_one:48.74 | Target_one:50.00
output_one:206.71 | Detected_one:48.74 | Target_one:50.00
output_one:207.82 | Detected_one:49.38 | Target_one:50.00
output_one:207.82 | Detected_one:49.38 | Target_one:50.00
output_one:207.12 | Detected_one:50.03 | Target_one:50.00
output_one:207.12 | Detected_one:50.03 | Target_one:50.00
output_one:207.32 | Detected_one:50.03 | Target_one:50.00
output_one:207.32 | Detected_one:50.03 | Target_one:50.00
output_one:208.36 | Detected_one:49.70 | Target_one:50.00
output_one:208.36 | Detected_one:49.70 | Target_one:50.00
output_one:208.36 | Detected_one:49.70 | Target_one:50.00
output_one:207.73 | Detected_one:50.03 | Target_one:50.00
output_one:207.73 | Detected_one:50.03 | Target_one:50.00
output_one:207.81 | Detected_one:50.03 | Target_one:50.00
output_one:207.81 | Detected_one:50.03 | Target_one:50.00
output_one:207.75 | Detected_one:50.03 | Target_one:50.00
output_one:207.75 | Detected_one:50.03 | Target_one:50.00
output_one:206.60 | Detected_one:50.35 | Target_one:50.00
output_one:206.60 | Detected_one:50.35 | Target_one:50.00
output_one:206.03 | Detected_one:50.35 | Target_one:50.00
output_one:206.03 | Detected_one:50.35 | Target_one:50.00
output_one:204.23 | Detected_one:50.67 | Target_one:50.00
output_one:204.23 | Detected_one:50.67 | Target_one:50.00
output_one:204.11 | Detected_one:50.35 | Target_one:50.00
output_one:204.11 | Detected_one:50.35 | Target_one:50.00
output_one:204.11 | Detected_one:50.35 | Target_one:50.00
output_one:202.19 | Detected_one:50.67 | Target_one:50.00
output_one:202.19 | Detected_one:50.67 | Target_one:50.00
output_one:202.07 | Detected_one:50.35 | Target_one:50.00
output_one:202.07 | Detected_one:50.35 | Target_one:50.00
output_one:201.24 | Detected_one:50.35 | Target_one:50.00
output_one:201.24 | Detected_one:50.35 | Target_one:50.00
output_one:200.54 | Detected_one:50.35 | Target_one:50.00
output_one:200.54 | Detected_one:50.35 | Target_one:50.00
output_one:202.04 | Detected_one:49.70 | Target_one:50.00
output_one:202.04 | Detected_one:49.70 | Target_one:50.00
output_one:201.27 | Detected_one:50.03 | Target_one:50.00
output_one:201.27 | Detected_one:50.03 | Target_one:50.00
output_one:202.45 | Detected_one:49.70 | Target_one:50.00
output_one:202.45 | Detected_one:49.70 | Target_one:50.00
output_one:202.45 | Detected_one:49.70 | Target_one:50.00
output_one:200.72 | Detected_one:50.35 | Target_one:50.00
output_one:200.72 | Detected_one:50.35 | Target_one:50.00
output_one:201.37 | Detected_one:50.03 | Target_one:50.00
output_one:201.37 | Detected_one:50.03 | Target_one:50.00
output_one:200.09 | Detected_one:50.35 | Target_one:50.00
output_one:200.09 | Detected_one:50.35 | Target_one:50.00
output_one:199.52 | Detected_one:50.35 | Target_one:50.00
output_one:199.52 | Detected_one:50.35 | Target_one:50.00
output_one:198.82 | Detected_one:50.35 | Target_one:50.00
output_one:198.82 | Detected_one:50.35 | Target_one:50.00
output_one:198.12 | Detected_one:50.35 | Target_one:50.00
output_one:198.12 | Detected_one:50.35 | Target_one:50.00
output_one:198.52 | Detected_one:50.03 | Target_one:50.00
output_one:198.52 | Detected_one:50.03 | Target_one:50.00
output_one:198.52 | Detected_one:50.03 | Target_one:50.00
output_one:197.24 | Detected_one:50.35 | Target_one:50.00
output_one:197.24 | Detected_one:50.35 | Target_one:50.00
output_one:197.77 | Detected_one:50.03 | Target_one:50.00
output_one:197.77 | Detected_one:50.03 | Target_one:50.00
output_one:198.68 | Detected_one:49.70 | Target_one:50.00
output_one:198.68 | Detected_one:49.70 | Target_one:50.00
output_one:199.14 | Detected_one:49.70 | Target_one:50.00
output_one:199.14 | Detected_one:49.70 | Target_one:50.00
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

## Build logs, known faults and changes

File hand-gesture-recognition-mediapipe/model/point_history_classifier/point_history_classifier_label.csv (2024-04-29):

Stop
Clockwise
Counter Clockwise
Move

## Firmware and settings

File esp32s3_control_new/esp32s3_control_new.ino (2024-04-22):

#include <Arduino.h>
#include <WiFi.h>
#include <ESPAsyncWebServer.h>
#include <ArduinoJson.h>
#include <unordered_map>
#include "Proj_Setup.h"

#define MOTOR_OFF_DELAY 2000
#define CONNECTION_TIMEOUT 100

// need to register to UIUC network
// const char * ssid = "The Retreat";
const char * ssid = "IllinoisNet_Guest";
const char * pass = NULL;

AsyncWebServer server(80); // use port 80, http

binState current_state = STOP;
long currentDuration = 0;
long recordTime = 0;

// web service handlers
void handleRoot(AsyncWebServerRequest *);
void handleStopMotors(AsyncWebServerRequest *);
void handleSetSpeed(AsyncWebServerRequest *);
void handleLid(AsyncWebServerRequest *);
void moveForwardBackward(AsyncWebServerRequest *);
void turnLeftRight(AsyncWebServerRequest *);
std::string stateToString(binState state);

void setup(void) {
	Serial.begin(9600);
    // Serial.println(WiFi.macAddress()); // MAC addr: 34:85:18:50:4B:54
    // long temp = millis();
    // while(millis() - temp < 2000);

	// wifi connection
    int counter = 0;
    bool serverTurnOn = true;
	WiFi.begin(ssid, pass);
	Serial.printf("Connecting to %s", ssid);
	while(!WiFi.isConnected()){ // attempt to connect
	    Serial.print(".");
	    delay(100);
        if(counter >= CONNECTION_TIMEOUT){
            Serial.println("Wifi connection failed");    
            serverTurnOn = false;
            break;
        }
        counter += 1;
	}
	Serial.println();
    
    if(serverTurnOn == false){ // if the connection fail, reboot esp32
        ESP.restart();
    }
    
	// output IP address for user connection
	Serial.println("WiFi IP: ");
	Serial.println(WiFi.localIP());

	// async server handling
	server.on("/", HTTP_GET, handleRoot);
	server.on("/stop_motors", HTTP_POST, handleStopMotors);
	server.on("/set_speed", HTTP_POST, handleSetSpeed);
    server.on("/set_lid", HTTP_POST, handleLid);
	server.on("/move", HTTP_POST, moveForwardBackward);
	server.on("/turn", HTTP_POST, turnLeftRight);

    // more services goes here
	server.begin();
	
	current_state = STOP;

    // motors setups
	stopDCMotor();
	setupMotorInterrupt();
    setupLinearActuator();
    QuickPID_Init();
	
	// for debug
	#if (DEBUG)
	setTargetTicksPerFrame(0,0);
	#endif

}

// main loop, cmd executing
void loop(void) {

	/* testing, debugging begin */
	#if (DEBUG)
	// plotData();
    // Serial.println("Hello");
	// checkLid();
    // Serial.println("Hello World");
	#endif

	/* testing, debugging end */
	switch(current_state){
		case LID: 
			// this event reject all the commands until this event finishes
			if(checkLid() == CLOSE){
				#if (DEBUG)
                Serial.println("Lid operation done");
				#endif
				current_state = STOP;
			}

			if(millis() - recordTime > MOTOR_OFF_DELAY){ // turn off h-bridges for dc motors when stop for 2000ms
				motorsOff();
			}

			break;
		case STOP:
			stopDCMotor(); // stop all DC motors

			if(millis() - recordTime > MOTOR_OFF_DELAY){ // turn off h-bridges for dc motors when stop for 2000ms
				motorsOff();
			}
            else{
                QuickPID_Compute();
            }

			break;

		case BACKWARD:
		case FORWARD:
		case LEFT:
		case RIGHT:
		case YOLO:
			QuickPID_Compute();
			// speedAutoAdjust();
			if(millis() - recordTime > currentDuration){

				#if (DEBUG)
                Serial.printf("Current Time: %d\n", millis());
                Serial.printf("Recorded Time: %d\n", recordTime);
				Serial.print(stateToString(current_state).c_str());
				Serial.println(" Done");
				#endif

				current_state = STOP;
				stopDCMotor();
                recordTime = millis();
			}
			break;
		default: break;
	}
}

/** web service handlers section **/
void handleRoot(AsyncWebServerRequest * request){

	#if (DEBUG)
	Serial.println("Request root");
	#endif

	request->send(200, "html", "<h1>Welcome to ESP32-S3</h1>");
}

/**
 * handleStopMotors()
 * the service handler for /stop_motors request, send stop control signals to the motors
 * @param request: a AsyncWebServerRequest object pointer
*/
void handleStopMotors(AsyncWebServerRequest * request){

	#if (DEBUG)
	Serial.println("Request stop");
	#endif

	JsonDocument doc;
	String response;	

	if(current_state == LID){

		#if (DEBUG)
		Serial.println("In LID state, motors have stop already");
		#endif

		doc["state"] = stateToString(LID);
		serializeJson(doc, response);
		request->send(200, "application/json", response);
		return;
	}

	stopDCMotor();

	// data to the client
	doc["state"] = stateToString(STOP);
	current_state = STOP;
	serializeJson(doc, response);

	recordTime = millis();
	request->send(200, "application/json", response);
}

/**
 * handleSetSpeed()
 * the service handler for /set_speed request, set the target speed for the motors 
 * @param request: a AsyncWebServerRequest object pointer
*/
void handleSetSpeed(AsyncWebServerRequest * request){
	
	#if (DEBUG)
	Serial.println("Request set speed");
	#endif

    JsonDocument doc;
    String response;

    // LID state, blocking commands
    if(current_state == LID){
		
		#if (DEBUG)
        Serial.println("BLOCK: lid is operating");
		#endif

    	doc["state"] = stateToString(LID);
        serializeJson(doc, response);
        request->send(200, "application/json", response);
        return;
    }

	// for other moving state
	float speedLeft = 0;
	float speedRight = 0;
	long duration = 0; // need to be miliseconds

	// get the control duration
	if(request->hasParam("duration", true)){
		duration = request->getParam("duration", true)->value().toInt();
		currentDuration = max(duration, (long)(0)); // guard negative values
	}

	// get the setting speed 
	if(request->hasParam("speedLeft", true)){
		speedLeft = request->getParam("speedLeft", true)->value().toFloat();
	}
	if(request->hasParam("speedRight",true)){
		speedRight = request->getParam("speedRight",true)->value().toFloat();
	}

	#if (DEBUG)
    Serial.printf("Left: %f, Right: %f, duration: %ld\n", speedLeft, speedRight, duration);
	#endif

	setTargetSpeed(speedLeft, speedRight);
	
	current_state = YOLO;
	doc["state"] = stateToString(current_state);
    serializeJson(doc, response);

	recordTime = millis(); // recording end time

    request->send(200, "application/json", response);
}

/**
 * handleLid()
 * the service handler for /set_lid request, set the lid to open
 * @param request: a AsyncWebServerRequest object pointer
*/
void handleLid(AsyncWebServerRequest * request){
	
	#if (DEBUG)
    Serial.println("Request lid operation");
	#endif

    JsonDocument doc;
	String response;
	
	// start operations
    stopDCMotor();
    setLid();

	// response data to the client
    current_state = LID;
	doc["state"] = stateToString(current_state);
	serializeJson(doc, response);

	recordTime = millis();
    request->send(200, "application/json", response);
}

/**
 * turnLeftRight()
 * the service handler for /turn request, turn the bin left or right
 * @param request: a AsyncWebServerRequest object pointer
*/
void turnLeftRight(AsyncWebServerRequest * request){
	#if (DEBUG)
	Serial.println("Request turn left or right");
	#endif

	JsonDocument doc;
	String response;

	// LID state, blocking commands
	if(current_state == LID){
		#if (DEBUG)
        Serial.println("BLOCK: lid is operating");
		#endif

		doc["state"] = stateToString(LID);
		serializeJson(doc, response);
		request->send(200, "application/json", response);
        return;
	}

	float speed = 0;
    long duration = 0;
	currentDuration = 5000;

	// get the control duration
	if(request->hasParam("duration", true)){
		duration = request->getParam("duration", true)->value().toInt();
		currentDuration = max(duration, (long)(0)); // guard negative values
	}

	// get the setting speed 
	if(request->hasParam("speed", true)){
		speed = request->getParam("speed", true)->value().toFloat();
	}

	// set the speed
	if(request->hasParam("direction", true)){
		String direction = request->getParam("direction", true)->value();
		if(direction == "left"){
			setTargetSpeed(-speed, speed);
			current_state = LEFT;
		}
		else if(direction == "right"){
			setTargetSpeed(speed, -speed);
			current_state = RIGHT;
		}
	}

	// setup response object
	doc["state"] = stateToString(current_state);
    
    #if (DEBUG)
    Serial.printf("duration: %ld, speed: %f, direction: ", duration, speed);
    Serial.print(stateToString(current_state).c_str());
    Serial.println();
	#endif

	// return different states
	serializeJson(doc, response);
	recordTime = millis();
	request->send(200, "application/json", response);
}

/**
 * moveForwardBackward()
 * the service handler for /move request, move the bin forward or backward
 * @param request: a AsyncWebServerRequest object pointer
*/
void moveForwardBackward(AsyncWebServerRequest * request){
	#if (DEBUG)
	Serial.println("Request move forward or backward");
	#endif

	JsonDocument doc;
	String response;

	// LID state, blocking commands
	if(current_state == LID){

        #if (DEBUG)
        Serial.println("BLOCK: lid is operating");
        #endif
		
		doc["state"] = stateToString(LID);
		serializeJson(doc, response);
		request->send(200, "application/json", response);
        return;
	}

	float speed = 0;
    long duration = 0;
	currentDuration = 5000;

	// get the control duration
	if(request->hasParam("duration", true)){
		duration = request->getParam("duration", true)->value().toInt();
		currentDuration = max(duration, (long)(0)); // guard negative values
	}

	// get the setting speed 
	if(request->hasParam("speed", true)){
		speed = request->getParam("speed", true)->value().toFloat();
	}

	// set the speed
	if(request->hasParam("direction", true)){
		String direction = request->getParam("direction", true)->value();
		if(direction == "forward"){
			setTargetSpeed(speed, speed);
			current_state = FORWARD;
		}
		else if(direction == "backward"){
			setTargetSpeed(-speed, -speed);
			current_state = BACKWARD;
		}
	}

	doc["state"] = stateToString(current_state);

	#if (DEBUG)
    Serial.printf("duration: %ld, speed: %f, direction: ", duration, speed);
    Serial.print(stateToString(current_state).c_str());
    Serial.println();
	#endif

	// return different states
	serializeJson(doc, response);
	recordTime = millis();
	request->send(200, "application/json", response);
}

/**
 * stateToString()
 * convert the binState enum to string
 * @param state: the binState enum
 * @return: the string representation of the binState
*/
std::string stateToString(binState state) {
    static const std::unordered_map<binState, std::string> stateMap = {
        {binState::LID, "LID"},
        {binState::STOP, "STOP"},
        {binState::BACKWARD, "BACKWARD"},
        {binState::FORWARD, "FORWARD"},
        {binState::LEFT, "LEFT"},
        {binState::RIGHT, "RIGHT"},
		{binState::YOLO, "YOLO"}
    };

    auto it = stateMap.find(state);
    if (it != stateMap.end()) {
        return it->second;
    } else {
        return "UNKNOWN";
    }
}

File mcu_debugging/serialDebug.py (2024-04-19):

import sys
import serial
from PyQt5.QtWidgets import QApplication, QMainWindow, QVBoxLayout, QWidget, QPushButton, QLineEdit, QTextEdit
from PyQt5.QtCore import QThread, pyqtSignal
from matplotlib.figure import Figure
from matplotlib.backends.backend_qt5agg import FigureCanvasQTAgg as FigureCanvas
import numpy as np

DEVICE_PATH = "/dev/cu.usbserial-10"
BAUD_RATE = 9600

class SerialThread(QThread):
    data_received = pyqtSignal(str)

    def __init__(self, port, baud_rate):
        super().__init__()
        self.port = port
        self.baud_rate = baud_rate
        self.running = True

    def run(self):
        with serial.Serial(self.port, self.baud_rate, timeout=1) as ser:
            while self.running:
                if ser.in_waiting:
                    data = ser.readline().decode().strip()
                    self.data_received.emit(data)

    def stop(self):
        self.running = False
        self.wait()

class MainWindow(QMainWindow):
    def __init__(self):
        super().__init__()
        self.setWindowTitle("Serial Data Plotter")
        
        self.main_widget = QWidget(self)
        self.setCentralWidget(self.main_widget)
        layout = QVBoxLayout(self.main_widget)

        self.figure = Figure()
        self.canvas = FigureCanvas(self.figure)
        layout.addWidget(self.canvas)
        self.ax = self.figure.add_subplot(111)
        self.ax.set_title("Real-time Data Plot")
        self.lines, = self.ax.plot([], [], '-')

        self.text_edit = QTextEdit()
        self.text_edit.setReadOnly(True)
        layout.addWidget(self.text_edit)

        self.line_edit = QLineEdit()
        layout.addWidget(self.line_edit)

        self.send_button = QPushButton("Send")
        self.send_button.clicked.connect(self.send_data)
        layout.addWidget(self.send_button)

        self.serial_thread = SerialThread(DEVICE_PATH, BAUD_RATE)
        self.serial_thread.data_received.connect(self.update_plot)
        self.serial_thread.start()

    def update_plot(self, data):
        try:
            # Assuming data is a comma-separated string of numbers
            numbers = list(map(float, data.split(',')))
            self.lines.set_xdata(np.append(self.lines.get_xdata(), len(self.lines.get_xdata())))
            self.lines.set_ydata(np.append(self.lines.get_ydata(), numbers))
            self.ax.relim()
            self.ax.autoscale_view(True,True,True)
            self.canvas.draw()
            self.text_edit.append(data)
        except ValueError:
            pass  # Ignore any conversion errors

    def send_data(self):
        data = self.line_edit.text() + '\n'
        self.serial_thread.serial.write(data.encode())
        self.line_edit.clear()

    def closeEvent(self, event):
        self.serial_thread.stop()
        super().closeEvent(event)

if __name__ == '__main__':
    app = QApplication(sys.argv)
    main = MainWindow()
    main.show()
    sys.exit(app.exec_())


# import sys
# import serial
# from PyQt5.QtWidgets import QApplication, QMainWindow, QVBoxLayout, QTextEdit, QLineEdit, QPushButton, QWidget
# from PyQt5.QtCore import QTimer, QThread, pyqtSignal, Qt
# import matplotlib
# from matplotlib.backends.backend_qt5agg import FigureCanvasQTAgg as FigureCanvas
# from matplotlib.figure import Figure
# matplotlib.use('Qt5Agg')

# LENGTH_LIMIT = 100
# DEVICE_PATH = "/dev/cu.usbserial-10"

# class SerialThread(QThread):
#     data_received = pyqtSignal(str)

#     def __init__(self, parent=None):
#         super().__init__(parent)
#         self.ser = None
#         self.data_dict = {}
#         self.running = False

#     def run(self):
#         self.running = True
#         try:
#             self.ser = serial.Serial(DEVICE_PATH, 9600, timeout=0.1)
#             while self.running:
#                 data = self.ser.readline().decode("utf-8").strip()
#                 if data:
#                     self.parse_data(data)
#                     self.data_received.emit(data)
#         except serial.SerialException as e:
#             print(f"Error opening serial port: {e}")
#         finally:
#             if self.ser:
#                 self.ser.close()

#     def parse_data(self, line):
#         pairs = line.split(', ')
#         for pair in pairs[:-1]:
#             if ':' in pair:
#                 name, value = pair.split(':', 1)
#                 if name not in self.data_dict:
#                     self.data_dict[name] = []
#                 if len(self.data_dict[name]) >= LENGTH_LIMIT:
#                     self.data_dict[name].pop(0)
#                 self.data_dict[name].append(float(value))

#     def write_data(self, message):
#         if self.ser:
#             self.ser.write(message.encode('utf-8'))

#     def stop(self):
#         self.running = False
#         self.wait()

# class MainWindow(QMainWindow):
#     def __init__(self):
#         super().__init__()
#         self.setWindowTitle("Serial Data Plotter")
#         self.resize(800, 600)

#         central_widget = QWidget()
#         layout = QVBoxLayout()

#         self.text_edit = QTextEdit()
#         layout.addWidget(self.text_edit)

#         self.figure = Figure()
#         self.canvas = FigureCanvas(self.figure)
#         layout.addWidget(self.canvas)

#         self.line_edit = QLineEdit()
#         layout.addWidget(self.line_edit)

#         send_button = QPushButton("Send")
#         send_button.clicked.connect(self.send_data)
#         layout.addWidget(send_button)

#         central_widget.setLayout(layout)
#         self.setCentralWidget(central_widget)

#         self.serial_thread = SerialThread()
#         self.serial_thread.data_received.connect(self.update_text)
#         self.serial_thread.start()

#         self.data_dict = self.serial_thread.data_dict
#         self.timer = QTimer()
#         self.timer.timeout.connect(self.update_plot)
#         self.timer.start(50)

#     def update_text(self, data):
#         self.text_edit.append(f"Received: {data}")

#     def update_plot(self):
#         self.figure.clear()
#         ax = self.figure.add_subplot(111)
#         for name, values in self.data_dict.items():
#             ax.plot(range(len(values)), values, label=name)
#         ax.legend()
#         ax.set_title("Live Data Plot")
#         ax.set_xlabel("Index")
#         ax.set_ylabel("Value")
#         self.canvas.draw()

#     def send_data(self):
#         message = self.line_edit.text()
#         self.serial_thread.write_data(message)
#         self.line_edit.clear()

#     def closeEvent(self, event):
#         self.serial_thread.stop()
#         event.accept()

# if __name__ == "__main__":
#     app = QApplication(sys.argv)
#     window = MainWindow()
#     window.show()
#     sys.exit(app.exec_())

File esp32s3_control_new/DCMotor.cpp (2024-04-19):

#include "DCMotor.h"

DCMotor::DCMotor(){}

// main motor object constructor
DCMotor::DCMotor(int D1, int D2, int PWM, int HALL_A, int HALL_B, int channel, int freq=200, int resol=8){
    mt_D1 = D1; 
    mt_D2 = D2;
    mt_HALL_A = HALL_A;
    mt_HALL_B = HALL_B;
    // mt_PWM = PWM;
    ledc_channel = channel;
    mt_resol = resol;
    mt_freq = freq;
    max_pwm = pow(2, resol)-1;
    pinMode(mt_D1, OUTPUT);
    pinMode(mt_D2, OUTPUT);
    pinMode(mt_HALL_A, INPUT_PULLUP);
    pinMode(mt_HALL_B, INPUT_PULLUP);
    ledcSetup(channel, mt_freq, mt_resol);
    ledcAttachPin(PWM, channel);
}

// destructor
DCMotor::~DCMotor(){}

// motor control logic
void DCMotor::motorCtrl(int pwmInput){
    // motor is not moving
    if(pwmInput == 0){
        digitalWrite(mt_D1, LOW);
        digitalWrite(mt_D2, LOW);
        return;
    }

    // determine the direction of rotation
    if(pwmInput > 0){
        digitalWrite(mt_D1, LOW);
        digitalWrite(mt_D2, HIGH);
        // MIN_PWM <= pwmIntA <= MAX_PWM
        ledcWrite(ledc_channel, constrain(pwmInput, 0, max_pwm));
    }
    else{
        digitalWrite(mt_D1, HIGH);
        digitalWrite(mt_D2, LOW);
        ledcWrite(ledc_channel, (-1)*constrain(pwmInput, -max_pwm, 0));
    }
    // ledcWrite(ledc_channel, constrain(abs(pwmInput), 0, max_pwm));
    // if(ccw){
    //     digitalWrite(mt_D1, LOW);
    //     digitalWrite(mt_D2, HIGH);
    //     // MIN_PWM <= pwmIntA <= MAX_PWM
    //     // ledcWrite(ledc_channel, constrain(pwmInput, 0, max_pwm));
    // }
    // else{
    //     digitalWrite(mt_D1, HIGH);
    //     digitalWrite(mt_D2, LOW);
    //     // ledcWrite(ledc_channel, (-1)*constrain(pwmInput, -max_pwm, 0));
    // }
}

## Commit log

2024-02-27 working on motor control scripts
2024-02-27 fixed a minor bug
    [Proj_Setup.cpp, Proj_Setup.h]
2024-02-27 some short pid control setup
    [Proj_Setup.cpp, Proj_Setup.h]
2024-02-28 simple PID
2024-03-03 working on control script, web+motor initial integration works fine
2024-03-04 Serial debugging for speed control, 6V DC motor works fine
2024-03-07 linear actuator control is done, need to test DC motors
2024-03-19 added motor h-bridge control for complete stop of the motors
2024-03-31 motor testing sample code
2024-03-31 uploaded testing files and testing data
    [pid_1s_p_1dot15_d_dot1.csv, pid_data.csv, pid_p_1dot1.csv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]
2024-04-09 added dev log for wireless communication
2024-04-11 added the IP address of the ESP32S3 on the customized PCB
2024-04-11 removed redundant notebook and updated note descripitons on wireless communication testing
2024-04-19 Mcu code (#1)
    * starting mcu code
    * working on motor control scripts
    * Update .gitignore
    * fixed a minor bug
    * some short pid control setup
    * simple PID
    * working on control script, web+motor initial integration works fine
    * Serial debugging for speed control, 6V DC motor works fine
    * make code more reusable
    * added some old code
    * linear actuator control is done, need to test DC motors
    * removed some redundant code and added some comments
    * updated control script
    * upload some debugging script
    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
    [pid_1s_p_1dot15_d_dot1.csv, pid_data.csv, pid_p_1dot1.csv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]
2024-04-19 Pcb design (#2)
    * upload esp32s3 basic circuits and extra components used in the circuit
    * version 2 of esp32-s3 circuit
    * added component footprints
    * upload power and motor driver schematics
    * upload combined circuit
    * updated circuit with interconncetion
    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
    [445_box_circuit_v1_new.3mf, 445_box_circuit_v3_new.3mf, 445_box_v1.stl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]
2024-04-19 changed folder name
    [pid_1s_p_1dot15_d_dot1.csv, pid_data.csv, pid_p_1dot1.csv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]
2024-04-19 updated folder name
    [pid_1s_p_1dot15_d_dot1.csv, pid_data.csv, pid_p_1dot1.csv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]
2024-04-22 Mcu code (#5)
    * updated notes
    * more responsive PID param
    * better PID adjustment
    [testing_left.csv, testing_left_adj.csv, testing_left_adj_2.csv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]
2024-04-22 merging Dongming's notes and minor PID graph changes (#6)
    * minor updated on the output graph
    * Dongming's notebook is done for now, might add some missing notes later
    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
2024-04-27 Mcu code (#7)
    * sync
    * Update README.md
    * some minor updates
    * minor updates
    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
2024-04-29 computer vision code from Owen (#8)
    [keypoint_classifier_label.csv, point_history.csv, point_history_classifier_label.csv]
2024-05-01 last version of pcb (from Josh)
